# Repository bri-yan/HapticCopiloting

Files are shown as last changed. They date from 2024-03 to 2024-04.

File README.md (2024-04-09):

# HapticCopiloting
Codebase for UBC's ENPH-459 (Engineering Physics) Capstone Project: **Haptic Shared Control**

Demonstrating complex human-robot control through a 1 DOF haptic device featuring a BDC motor control system in live feedback with a virtual environment.

Authors: 
* Gavin Pringle
* Yousif El-Wishahy
* Sayeh Oloumi Yazdi
* Brian Yan

## Important Directories
- twiddlerino: source code for the ESP32 controller, python serial interface, unit tests and test scripts
- sim: MATLAB source code for modelling and simualtion of motor, sensors and controller
- virtual_demos : directory containing virtual demonstrations for shared control, demos implemented in pygame and interface with esp32 controller using the serial interface
- electrical: KiCad pcb project (libraries, schematics and layout) using the twiddlerino hardware, and the KiCad electrical schematic for the test bench

## Contents
 - [Project Overview](#project-overview) 
 - [Firmware Dev Environment](#firmware-dev-environment) 

## Project Overview

When dancing with a partner, forces and torques from each person influence the motion of the other. Each person’s motion is therefore partially controlled by themselves and partially controlled by their partner. 

This is similar to shared control of a robotic system, where the behaviour of a robot changes depending on the stiffness of the environment it is operating in. In our project, we explore shared control on simple robotic devices with the addition of a virtual environment that guides the user on when to give and when to take control.

### Twiddlerino System Diagram

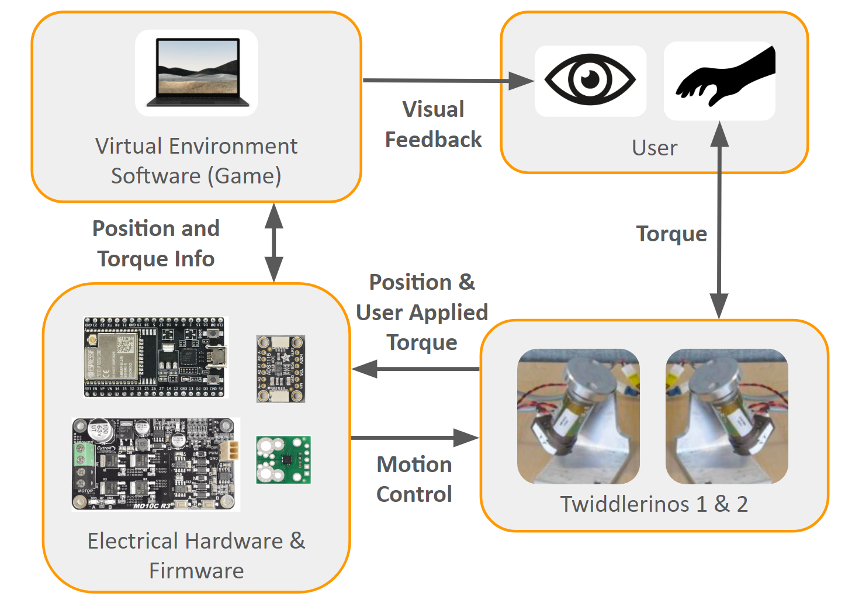
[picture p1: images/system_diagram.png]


### Control Theory

We have implemented shared control between a human and a robot by shifting between two existing controllers: impedance controllers and admittance controllers. Impedance and admittance controllers both simulate virtual spring-mass-damper systems. By shifting between these two controllers, the combined shared controller can act resistively and prevent changes to its trajectory or act compliantly and allow a person to dictate its trajectory.

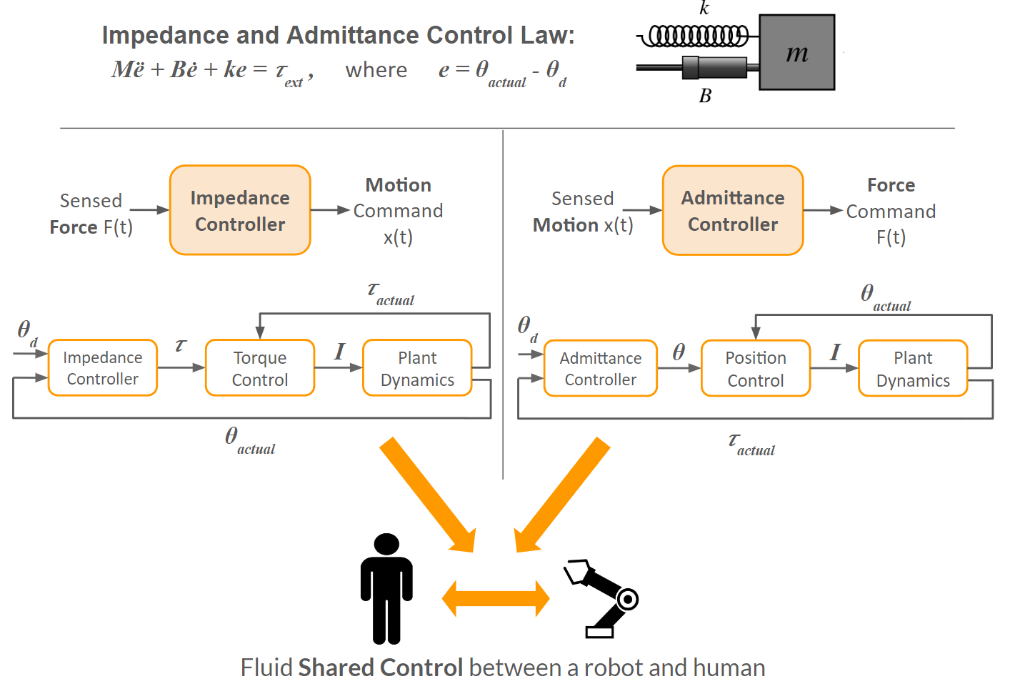
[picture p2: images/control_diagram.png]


### Defined Control Modes

Defined in control_type_t enum in the firmware:

| Control ID | Description |
|---|---|
| no_control | No actuator control is applied. Only telemetry is report. |
| position | Position PID control. Feedback is incremental encoder signal. |
| velocity | Velocity PID control. Feedback is rate of change of encoder signal. |
| torque | Current PID control to achieve torque control, uses linear relationship between current and torque.<br>Feedback is current sensor measurements. |
| impedance_spring | Cascaded controller. Inner loop runs current control with PID. <br>Outer loop applies a spring impedance law to determine desired current. <br>The linear friction torque (scales with velocity) is also accounted for in the impedance control law. |
| impedance_damping | Similar to imedance_spring but uses imedance damper law to compute current target. |
| impedance_spring_damping | Applies spring and damping impedance law. Has the effect of position and velocity impedance control. |
| impedance_ignore_t_ext | Applies full impedance law, but ignores external torques. |
| impedance | Applies full impedance law, and accounts for external torques.<br>External torque is estimated by comparing current measurements to an internal model the motor that estimates control current. |
| admittance | Applies full admittance law. This controller is also a cascaded controller.<br>The inner loop runs PID position control.<br>The outer loop runs an impedance control law to compute position. |

### Virtual Environment
The virtual environment guides the user on when to give and when to take control. The player  must control two twidderinos to ensure both player-controlled ships avoid all obstacles. Ships will automatically avoid asteroids but players must take action to avoid enemy projectiles.

Promoted Behaviour:
* Human-robot collaboration
* Shared common goal
* Awareness of robots actions

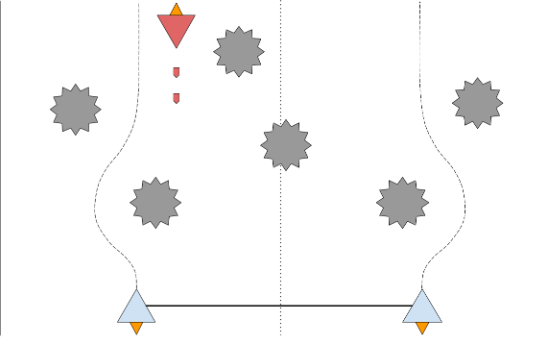
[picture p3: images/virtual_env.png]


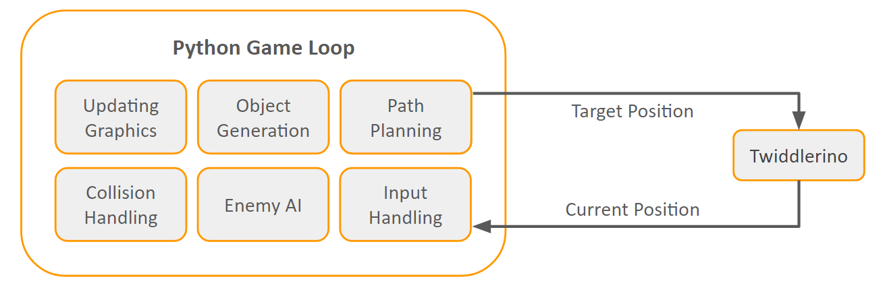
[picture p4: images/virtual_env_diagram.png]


### Hardware Architecture

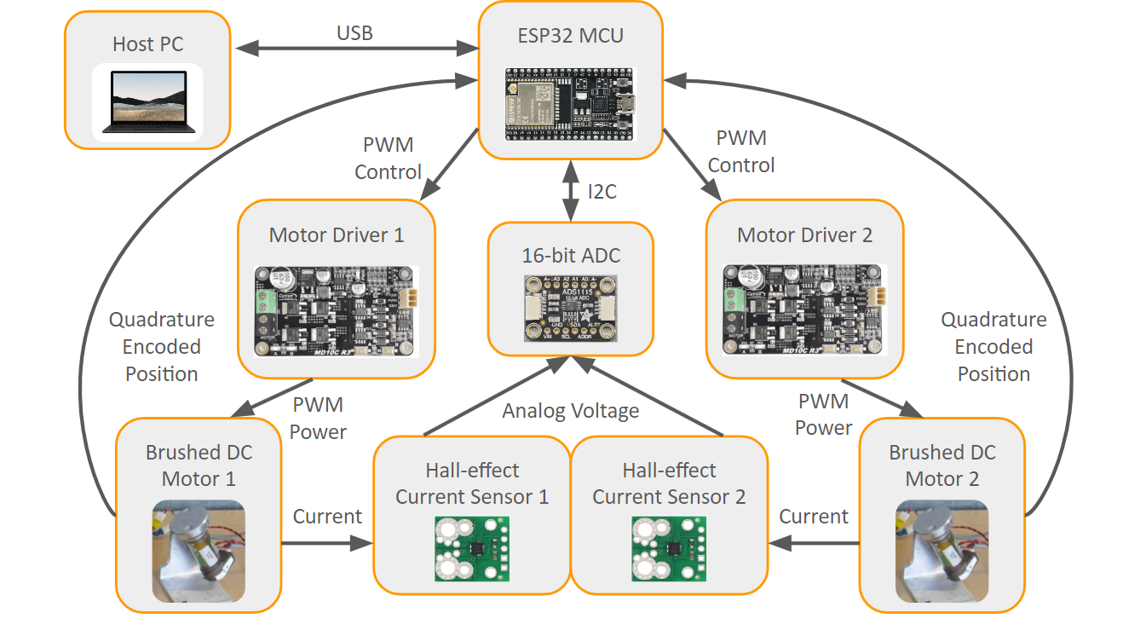
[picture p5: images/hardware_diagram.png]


### Firmware Architecure

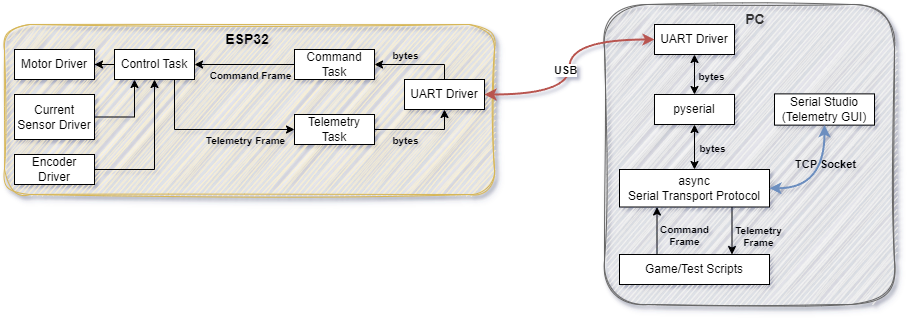
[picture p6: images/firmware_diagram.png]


## Firmware Dev Environment

[Refer to firmware diagram](#firmware-architecture)

Embedded development environment: [Platformio](https://platformio.org/) IDE plugin for VSCode

[Install platformio](https://platformio.org/)

config file: `twiddlerino/platformio.ini`

Directory structure

```bash
├───.pio
│   ├───build
│   └───libdeps
├───include
├───lib
├───python_tests
│   ├───data
│   └───serial_interface
├───src
│   ├───app
│   │   ├───calibration
│   │   ├───control
│   │   └───filter
│   └───drivers
└───test
```

## Serial Commmand & Telemetry Interface

Command and telemetry of the Twiddlerino system is achieved through telemetry and command frames (utf-8 encoded strings) sent over a USB port between the ESP32 and the HOST PC.

The ESP32 devkit has an onboard CP210X USB-to-UART module that converts the USB signal to a UART signal for the UART driver on the ESP32 to handle.

The serial protocol is implemented in C++ on esp32 and Python on Host PC.

[Refer to firmware diagram for details](#firmware-architecture)

### Telemetry Definition

[Serial Studio](https://serial-studio.github.io/), an open source telemetry GUI, is used to record and visualize system data during testing of the controller.

Telemetry frames are defined in a .JSON configuration file per the serial studio standard, see `twiddlerino/serial-studio-dashboard.json`.

Telemetry frame: `"/*TWIDDLERINO_TELEMETRY,%s,%s,...,%s*/"`

The firmware running on the ESP32 periodically sends telemetry strings over a serial port. The python serial protocol recieves the telemetry frames and sends them over a TCP socket to Serial Studio. 

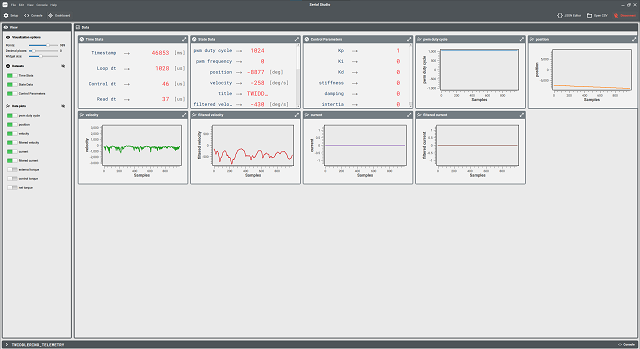
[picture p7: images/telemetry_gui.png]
Telemetry GUI


### Command Definition
Several commands are available to set parameters over the serial interface and to control the state of the controller.
**Each command is a newline terminated string.**

`"stop\n"` - Stops controller (telemetry also stops)

`"reset\n"` - Resets controller (configuration reverts to default)

`"reboot\n"` - Reboots the microcontroller! UART driver will not be affected.

`"telemetry_enable\n"` - Enable controller telemetry stream over serial (rate==`TELEMETRY_SAMPLES_PER_LOOP `)

`"telemetry_disable\n"` - Disable controller telemetry stream over serial (rate==`TELEMETRY_SAMPLES_PER_LOOP `)

`"set_pid,<controller_id(string)>,<double>,<double>,<double>,\n"` - Set P, I, and D values of PID controller

`"set_impedance,<controller_id(string)>,<double>,<double>,<double>,\n"` - Set stiffness, damping, and inertia values of impedane/admittance controller

`"set_mode,<controller_id(string)>,<string>,\n"` - Sets control mode, the string values represents an enum. Refer to the `control_type_t` struct definition in `twiddlerino/src/app/control/twid_control.h`.
* modes: `no_control`, `position`, `velocity`, `torque`, `impedance`, `impedance_spring`, `impedance_damping`, `impedance_spring_damping`, `impedance_ignore_t_ext`, `admittance`

`"set_setpoint,<controller_id(string)>,<double>,<double>,<double>,<double>,\n"` - Set position, velocity, acceleration and torque setpoints for the controller. 

`"set_dutycycle,<controller_id(string)>,<int>,\n"` - Sets motor duty cycle directly regardless of controller running.

`"set_telemsamplerate,<controller_id(string)>,<uint>,\n"` - Set telemetry sample rate in terms of (# control loops)/sample. I.e. how many control loops to wait before sending telemetry to serial queue.

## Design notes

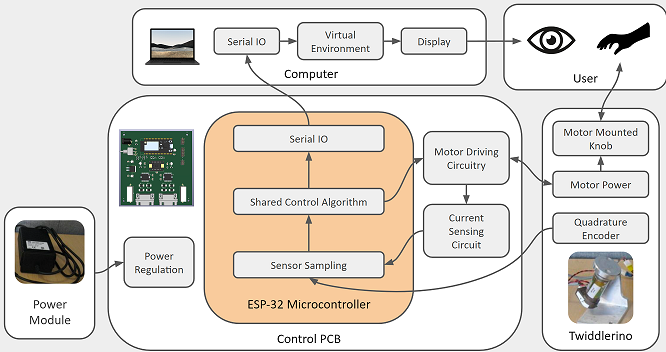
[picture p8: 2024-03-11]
system_diagram.png

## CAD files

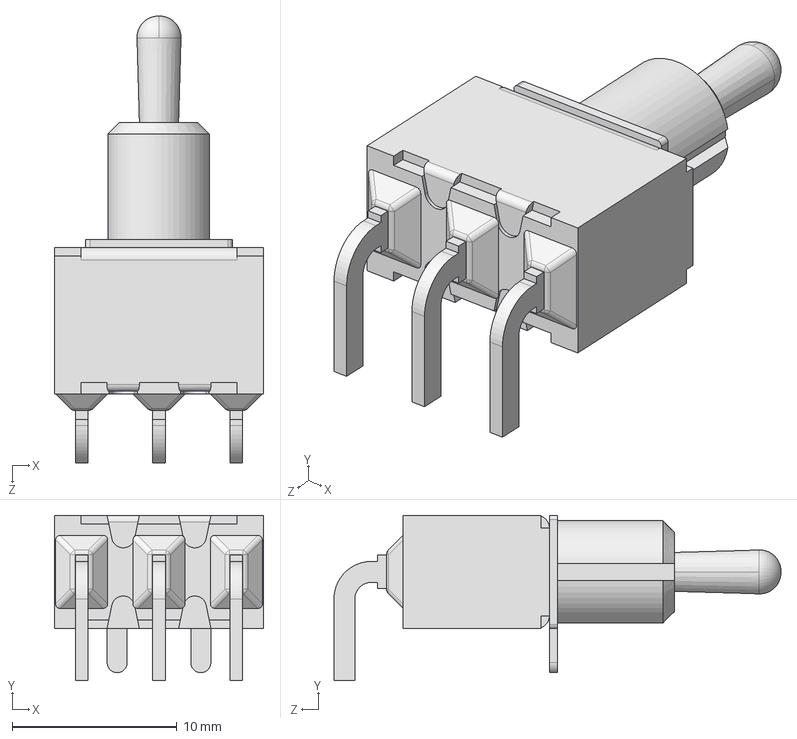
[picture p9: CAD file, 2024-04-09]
electrical/component_libs/100SP1T2B4M6QE/100SP1T2B4M6QE.step
12.7 x 10.0 x 27.2 mm

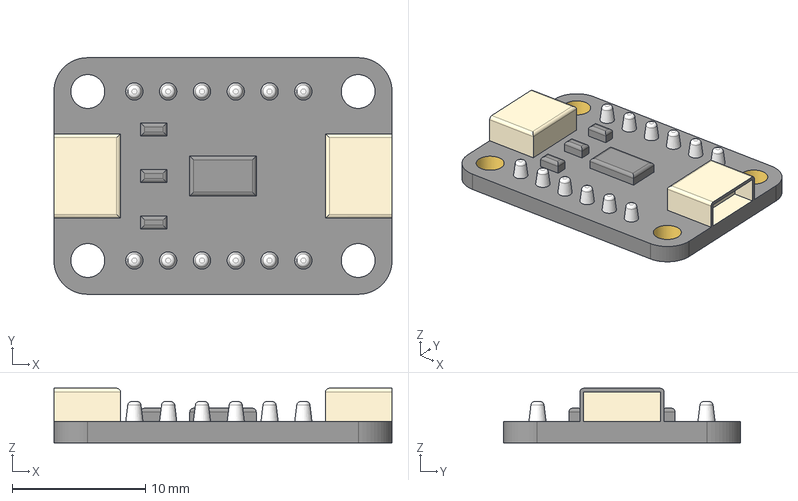
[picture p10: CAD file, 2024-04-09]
electrical/component_libs/adafruit_ads1115/adafruit_ads1115.step
25.4 x 17.8 x 4.10 mm

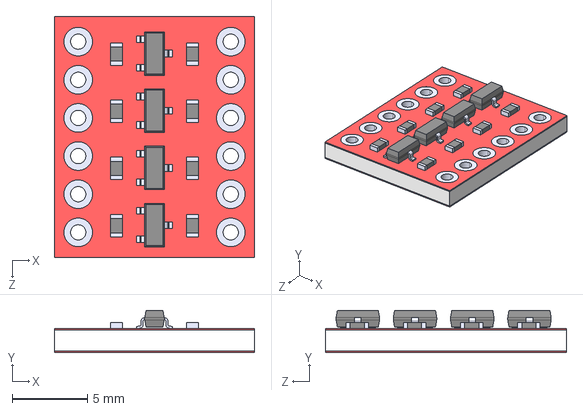
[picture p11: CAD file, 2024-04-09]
electrical/component_libs/BOB-12009/BOB-12009.step
13.3 x 2.80 x 16.1 mm

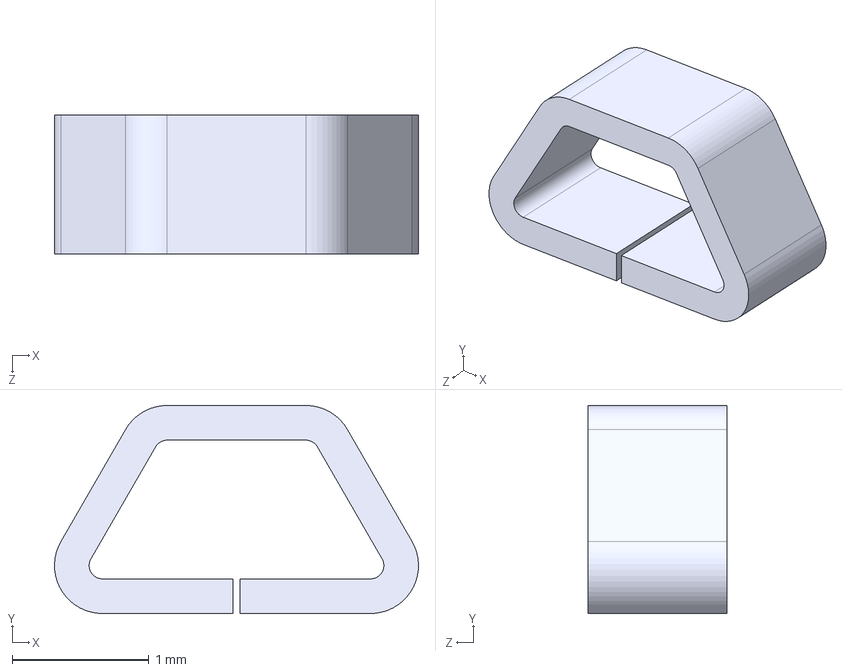
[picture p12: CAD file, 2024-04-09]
electrical/component_libs/Keystone5015/Keystone5015.STEP
2.67 x 1.52 x 1.02 mm

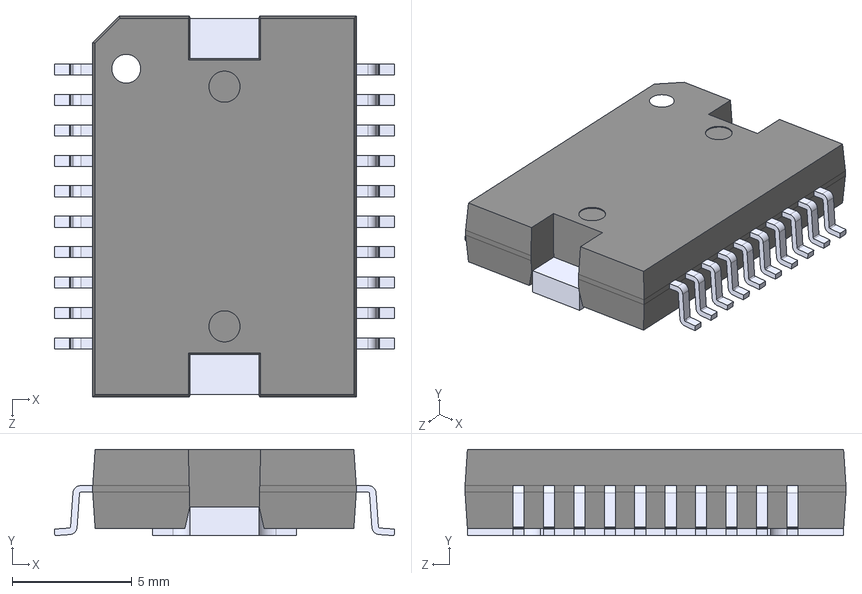
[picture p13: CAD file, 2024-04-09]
electrical/component_libs/L298P/L298P.step
14.2 x 3.60 x 15.9 mm

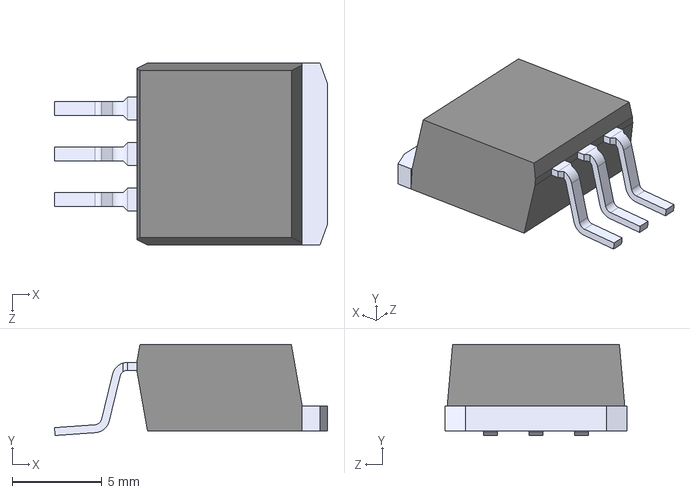
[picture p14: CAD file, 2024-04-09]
electrical/component_libs/LM340S-5/LM340S-5.step
15.2 x 5.08 x 10.2 mm

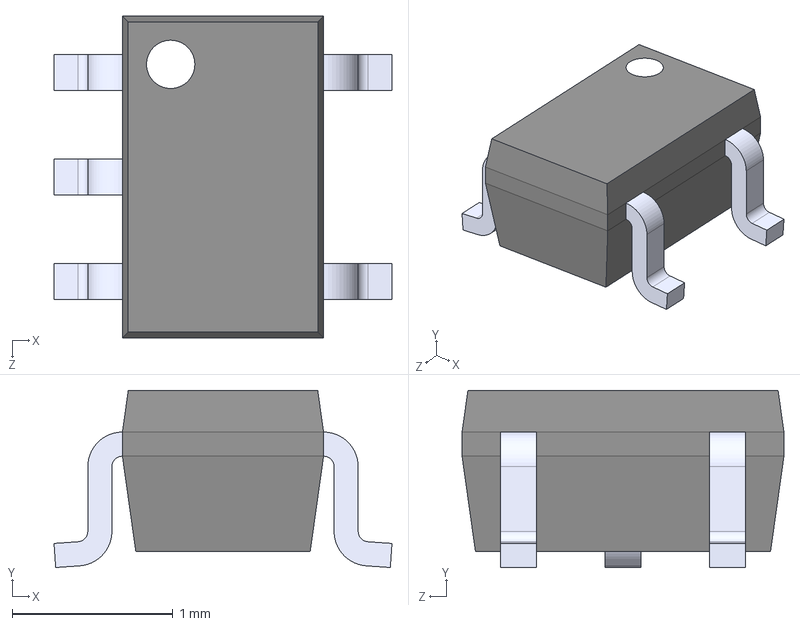
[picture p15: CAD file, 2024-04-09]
electrical/component_libs/OPA347SA_3K/OPA347SA_3K.step
2.10 x 1.10 x 2.00 mm

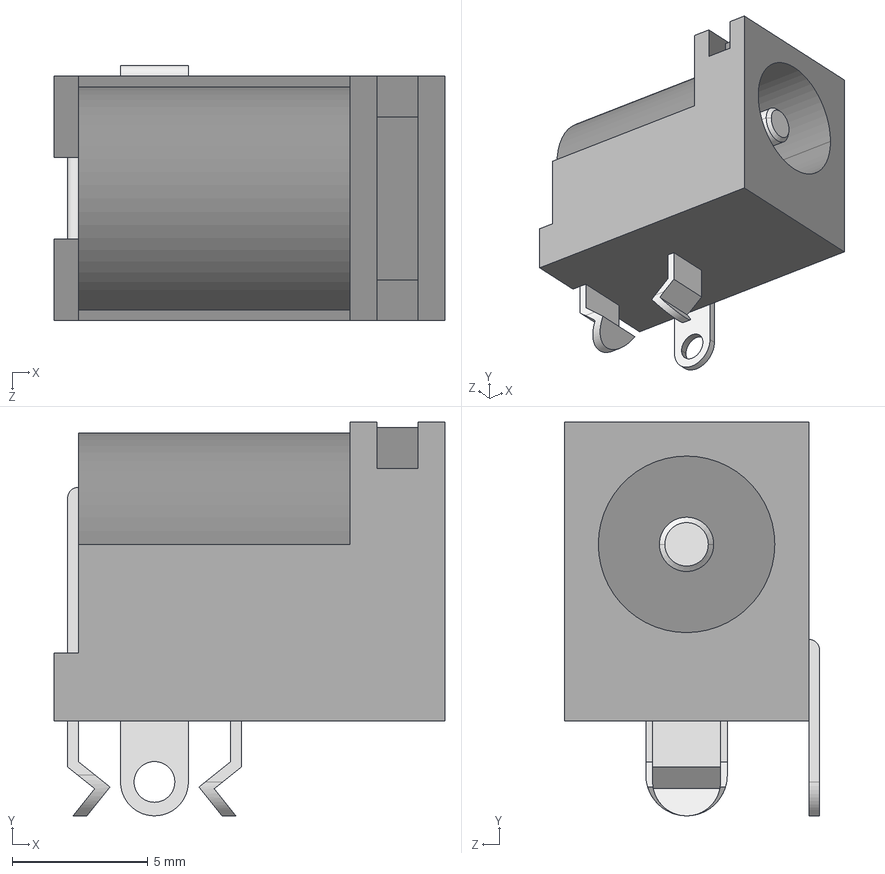
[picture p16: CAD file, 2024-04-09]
electrical/component_libs/PJ-202AH/CUI_DEVICES_PJ-202AH.step
14.4 x 14.5 x 9.40 mm

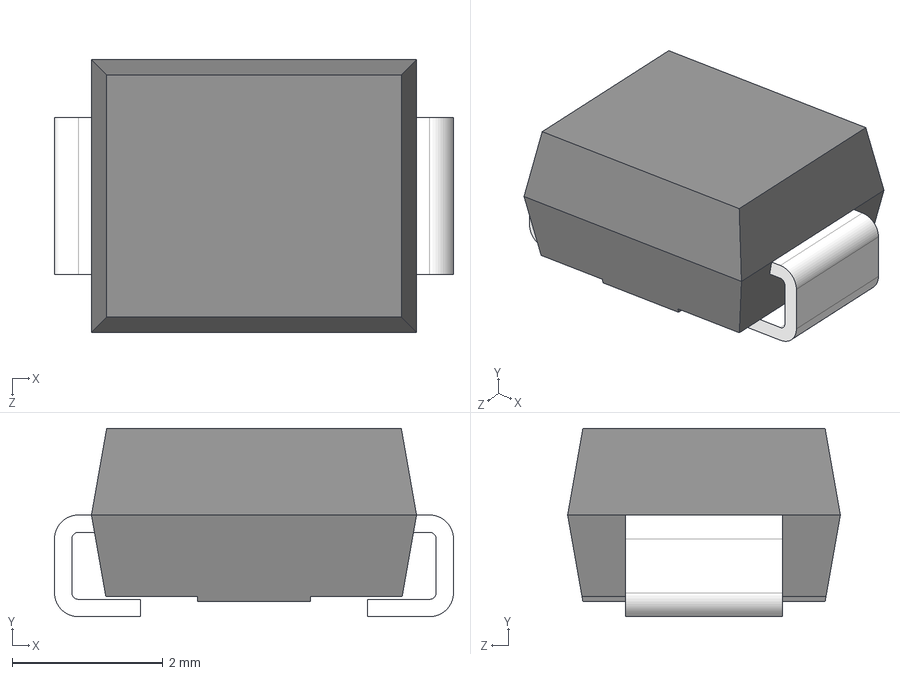
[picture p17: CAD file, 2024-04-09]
electrical/component_libs/RS3A-13-F/RS3A-13-F.step
5.30 x 2.50 x 3.62 mm

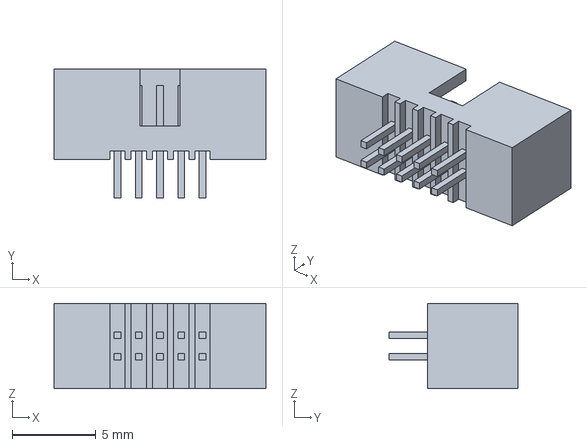
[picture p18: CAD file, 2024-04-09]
electrical/component_libs/20021511-00010T4LF/20021511-00010T4LF.step
12.7 x 7.70 x 5.10 mm

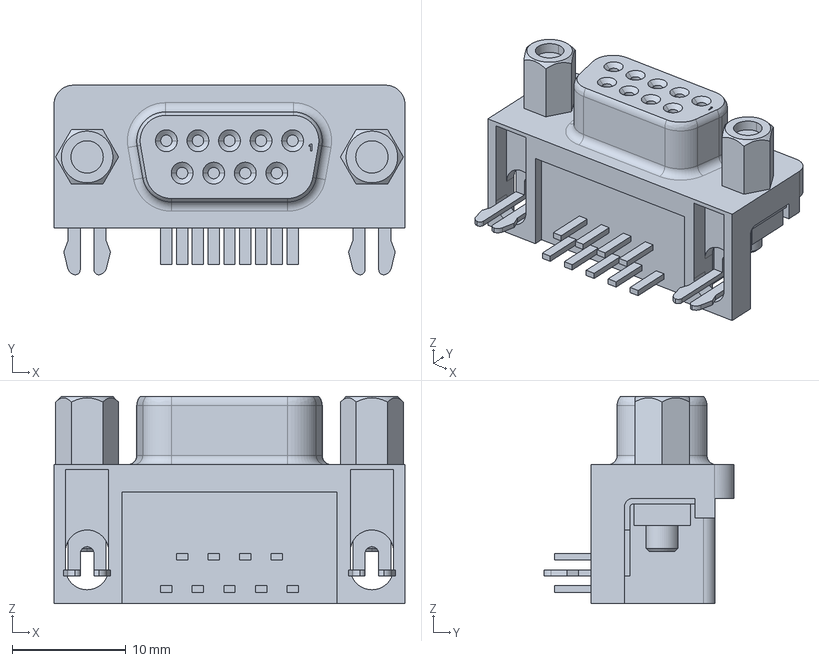
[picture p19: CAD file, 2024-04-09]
electrical/component_libs/2311765-1/2311765-1.step
30.8 x 16.6 x 18.2 mm

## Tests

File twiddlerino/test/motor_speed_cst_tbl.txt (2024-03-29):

dc
490.0,
495.0,
500.0,
506.0,
511.0,
516.0,
522.0,
527.0,
533.0,
538.0,
543.0,
549.0,
554.0,
560.0,
565.0,
570.0,
576.0,
581.0,
587.0,
592.0,
597.0,
603.0,
608.0,
614.0,
619.0,
624.0,
630.0,
635.0,
641.0,
646.0,
651.0,
657.0,
662.0,
668.0,
673.0,
678.0,
684.0,
689.0,
694.0,
700.0,
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
volts_approx
5.7421875,
5.80078125,
5.859375,
5.9296875,
5.98828125,
6.046875,
6.1171875,
6.17578125,
6.24609375,
6.3046875,
6.36328125,
6.43359375,
6.4921875,
6.5625,
6.62109375,
6.6796875,
6.75,
6.80859375,
6.87890625,
6.9375,
6.99609375,
7.06640625,
7.125,
7.1953125,
7.25390625,
7.3125,
7.3828125,
7.44140625,
7.51171875,
7.5703125,
7.62890625,
7.69921875,
7.7578125,
7.828125,
7.88671875,
7.9453125,
8.015625,
8.07421875,
8.1328125,
8.203125,
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
current
0.159187,
0.133125,
0.1395,
0.136688,
0.131625,
0.133313,
0.144562,
0.155062,
0.143063,
0.1485,
0.143813,
0.144375,
0.15225,
0.1545,
0.153563,
0.164625,
0.162375,
0.15525,
0.168938,
0.16125,
0.162938,
0.167438,
0.17175,
0.178125,
0.178312,
0.175125,
0.17325,
0.179438,
0.178875,
0.180375,
0.183375,
0.178312,
0.18375,
0.182625,
0.190313,
0.186937,
0.192188,
0.19125,
0.192938,
0.193687,
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
vel_filtered
12.968628837354,
24.3714350746476,
33.2487898171962,
41.5701308022924,
49.8356703758814,
57.6959549001702,
66.1900503590898,
74.36253790807501,
83.0116520766108,
91.377109419051,
99.9637825218804,
108.49980967367641,
116.746442820414,
125.1817082664906,
133.8068142689586,
141.9745308885756,
151.1072048604606,
159.0463129206876,
167.3490344111844,
175.8605258185602,
183.9147956042046,
193.2027904023288,
202.2435127452684,
211.4056059647268,
220.346972465262,
229.5234294713676,
238.73276116428718,
247.52061273153421,
255.99656967389578,
263.483626338357,
271.67072732599263,
279.3544512306072,
287.6387007767028,
297.29117828415656,
307.3967208750402,
317.1400195611984,
328.2603700037826,
338.6205349137336,
348.95609454531717,
360.9387905497434,
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
i_rpm
v_rpm
Ke
38.11784627294291,
R
0.0030723654445421814,

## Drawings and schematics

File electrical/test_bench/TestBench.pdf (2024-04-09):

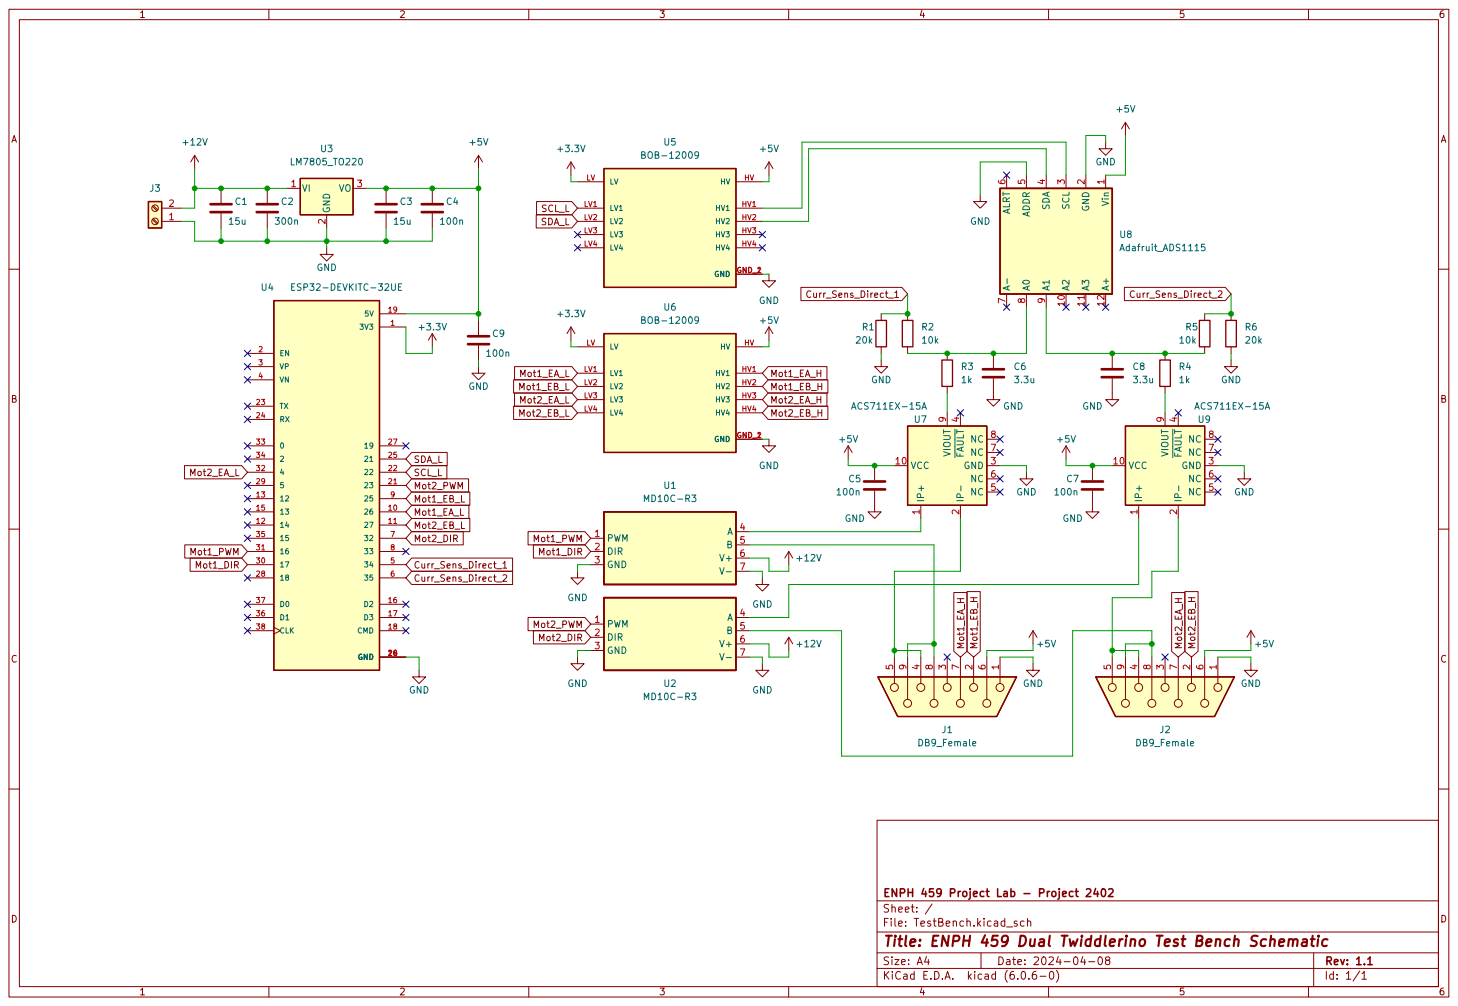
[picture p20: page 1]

4 NC 5 NC 6 NC 7 NC 8 VIOUT U7 9 ACS711EX-15A
+5VGND

4 NC 5 NC 6 NC 7 NC 8 VIOUT

1 VCC 10 IP- 2 GND ~{FAULT} 3

Id: 1/1 Title: ENPH 459 Dual Twiddlerino Test Bench Schematic

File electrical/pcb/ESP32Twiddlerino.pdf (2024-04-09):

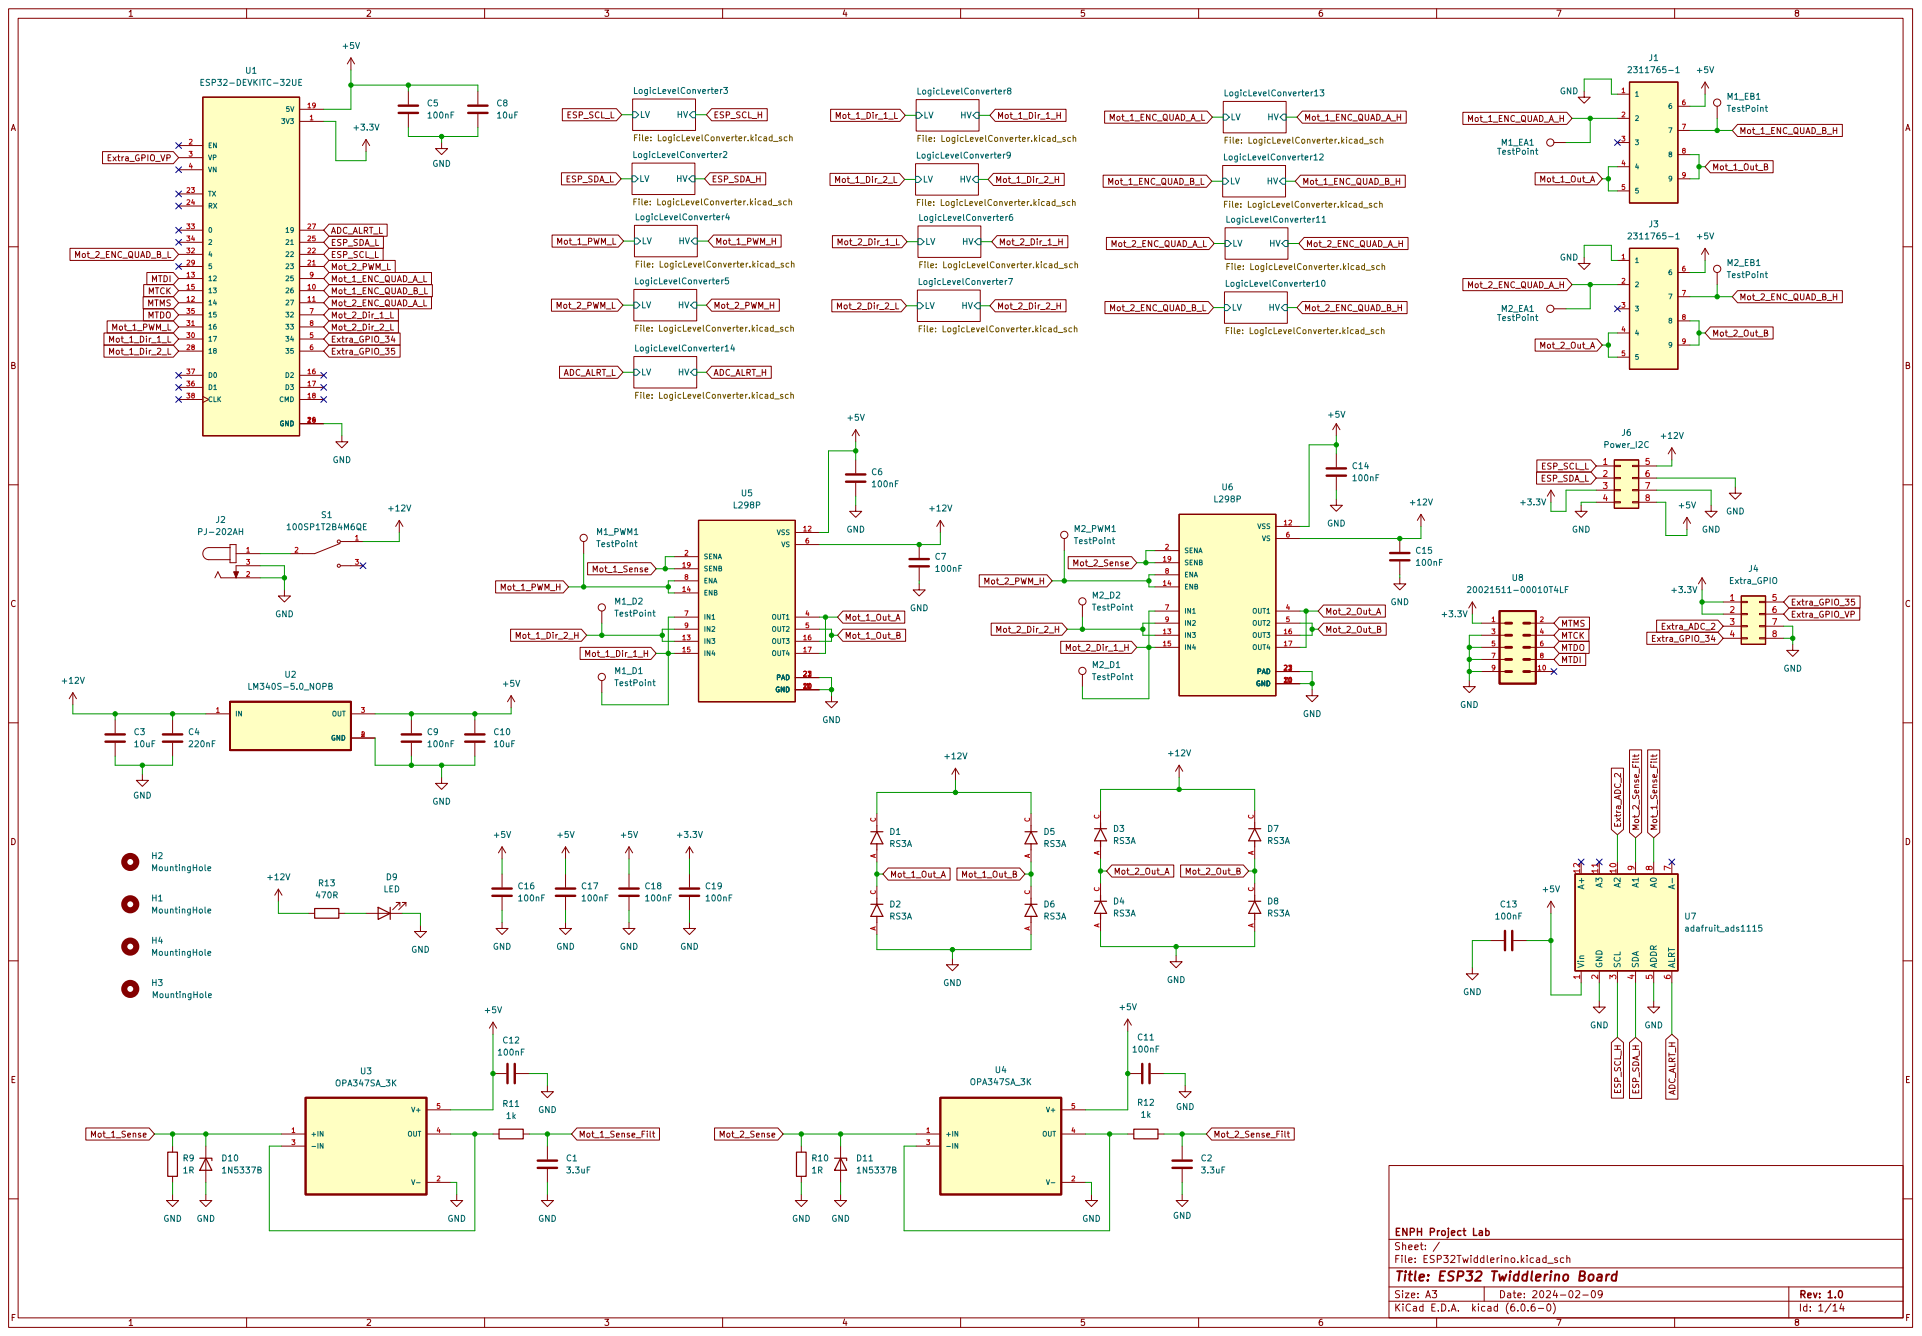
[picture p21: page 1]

File: ESP32Twiddlerino.kicad_sch Sheet: / ENPH Project Lab

Id: 1/14 Title: ESP32 Twiddlerino Board

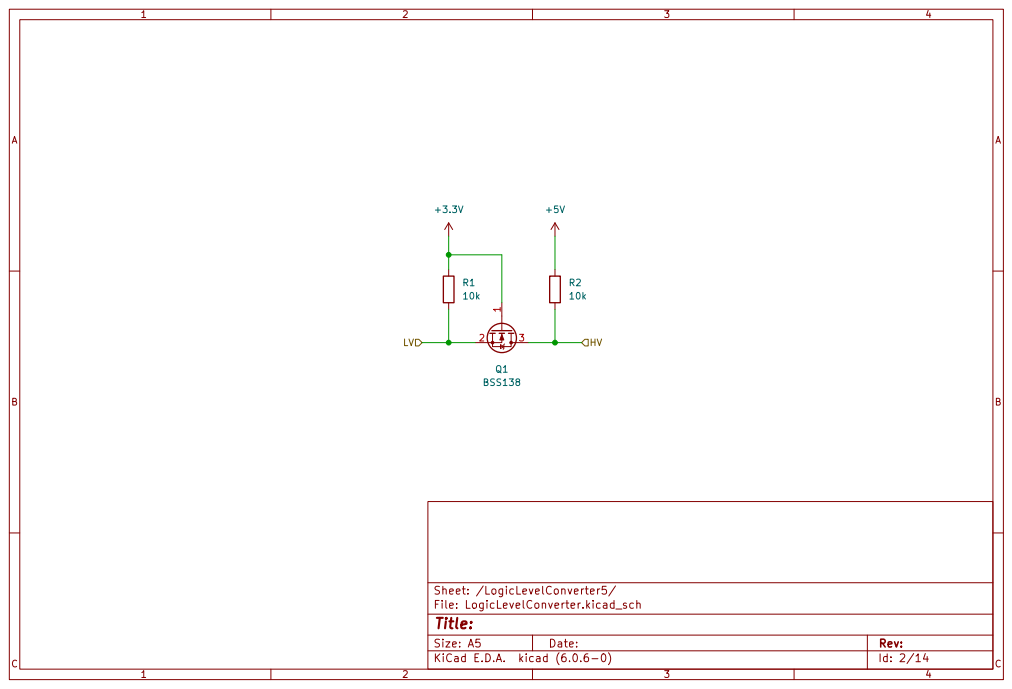
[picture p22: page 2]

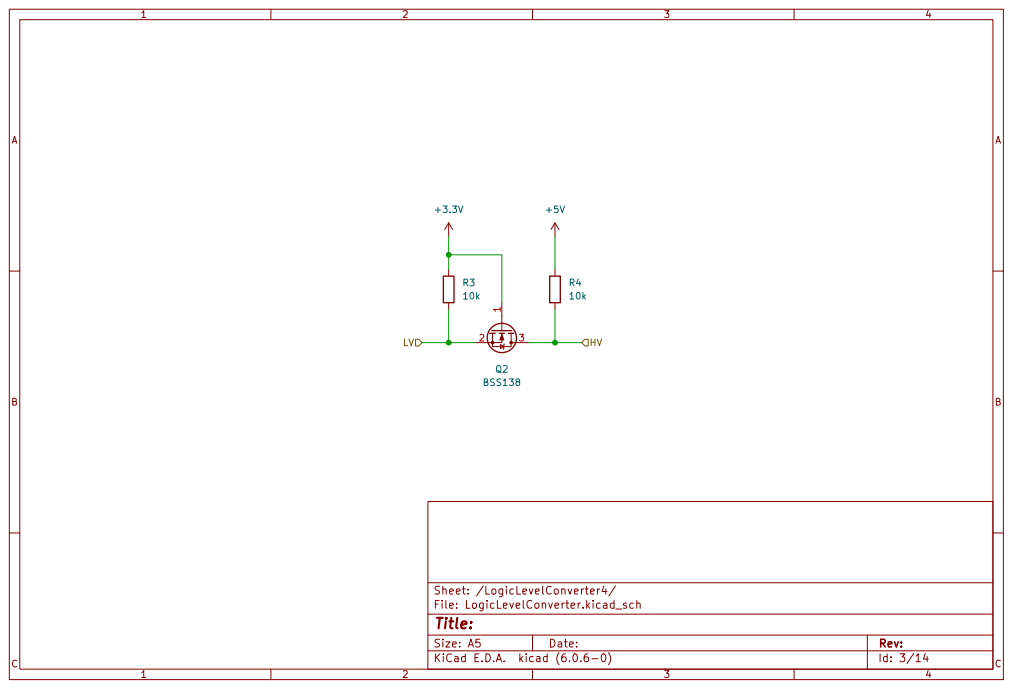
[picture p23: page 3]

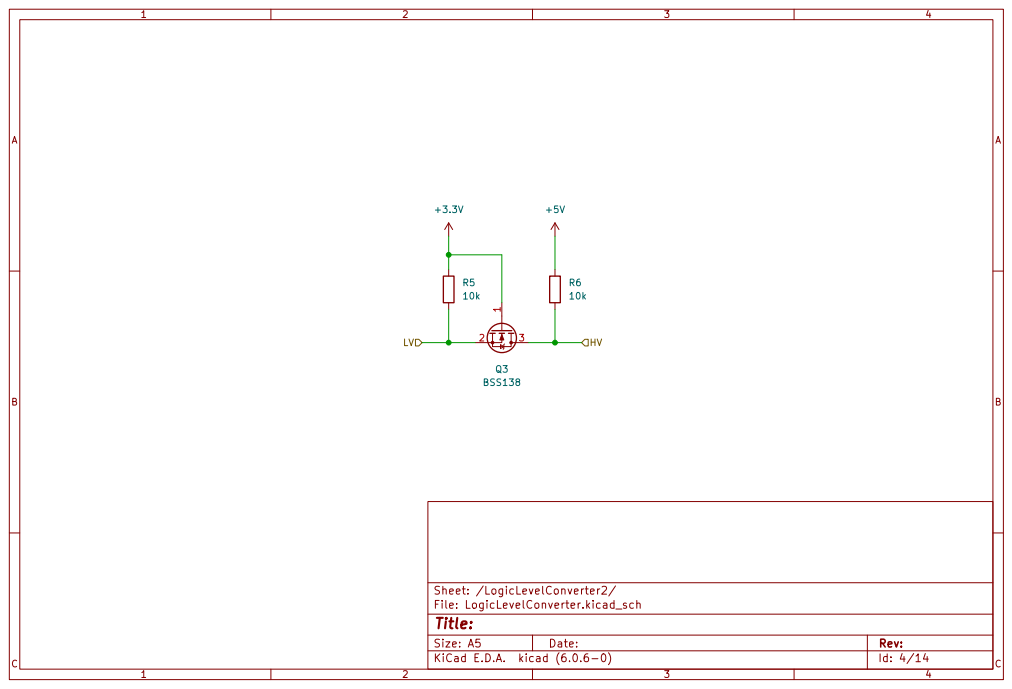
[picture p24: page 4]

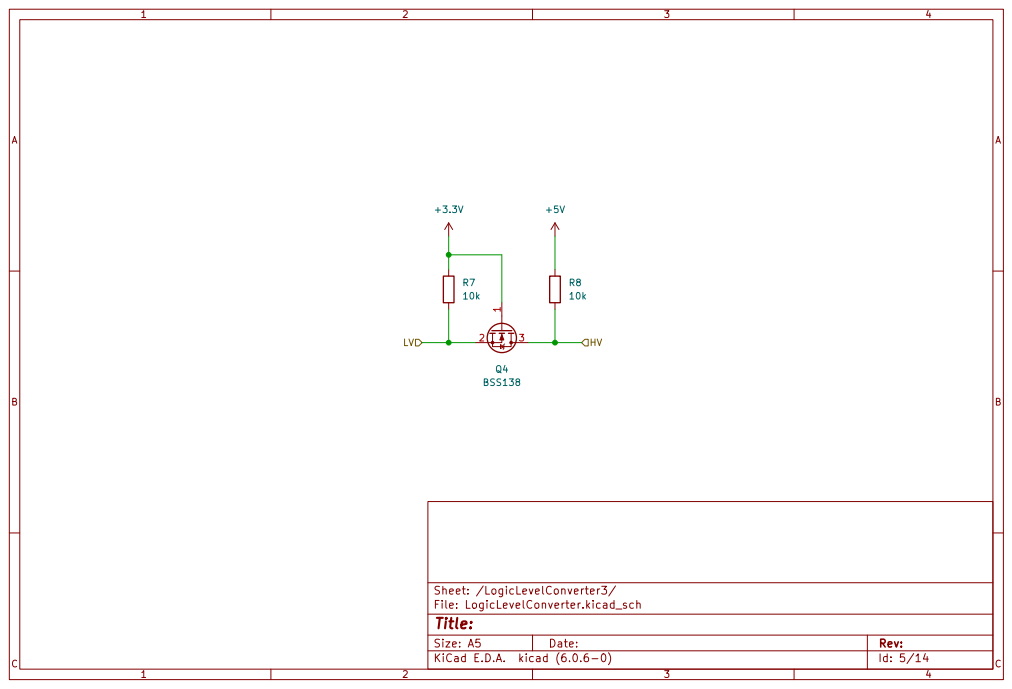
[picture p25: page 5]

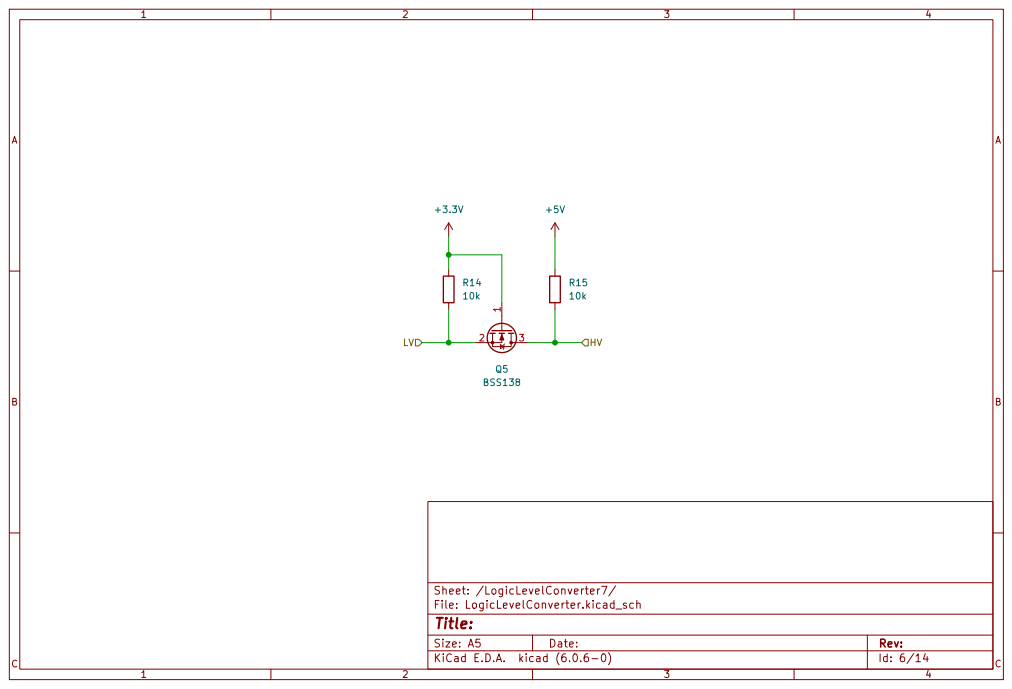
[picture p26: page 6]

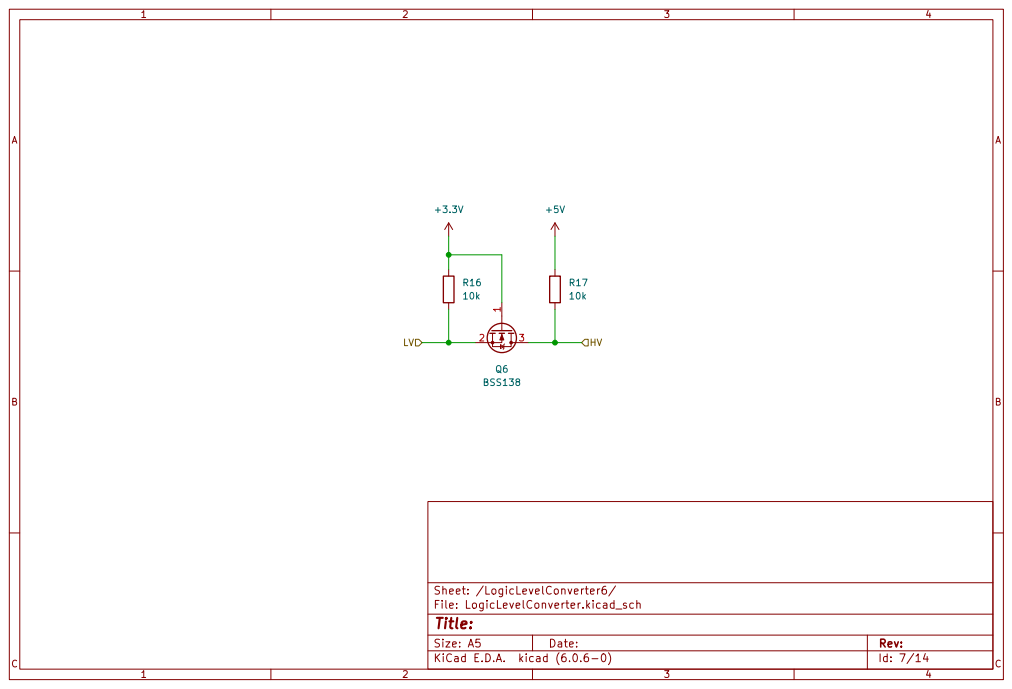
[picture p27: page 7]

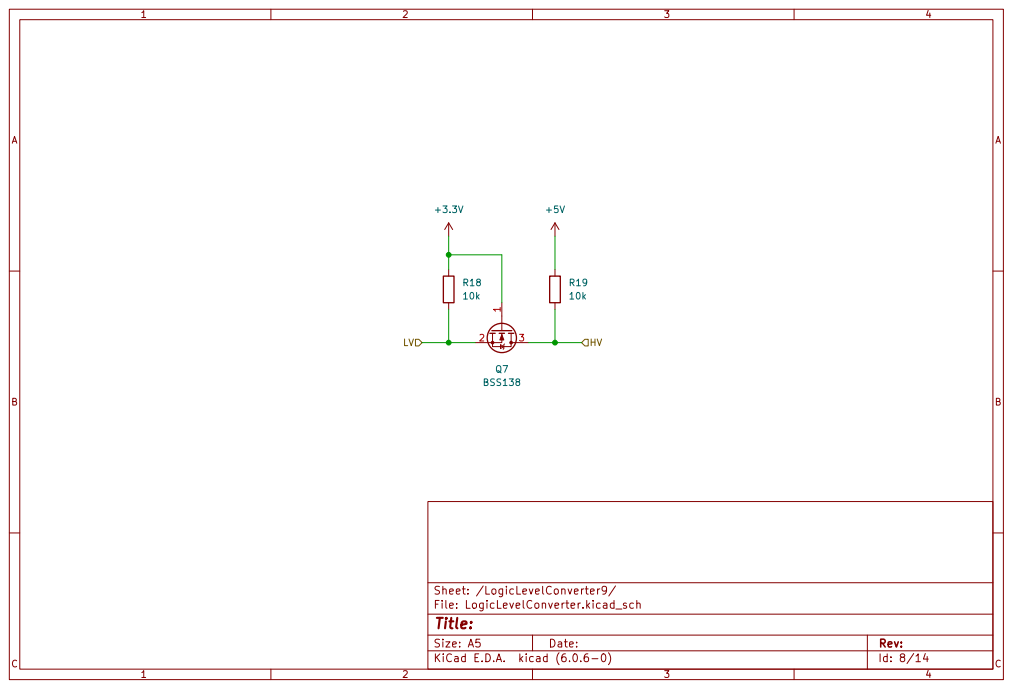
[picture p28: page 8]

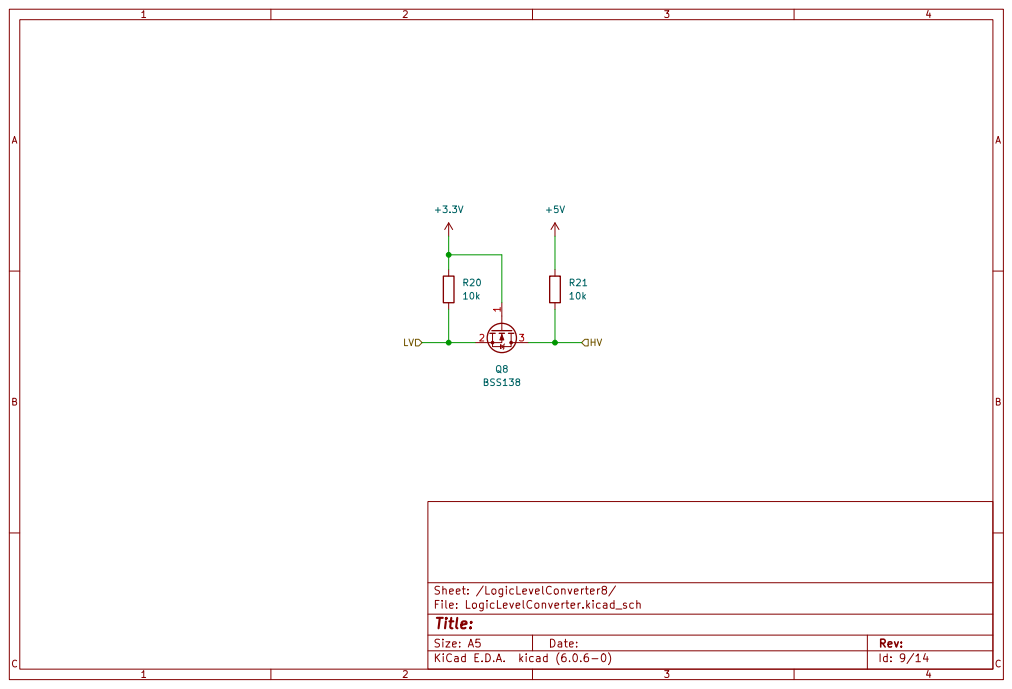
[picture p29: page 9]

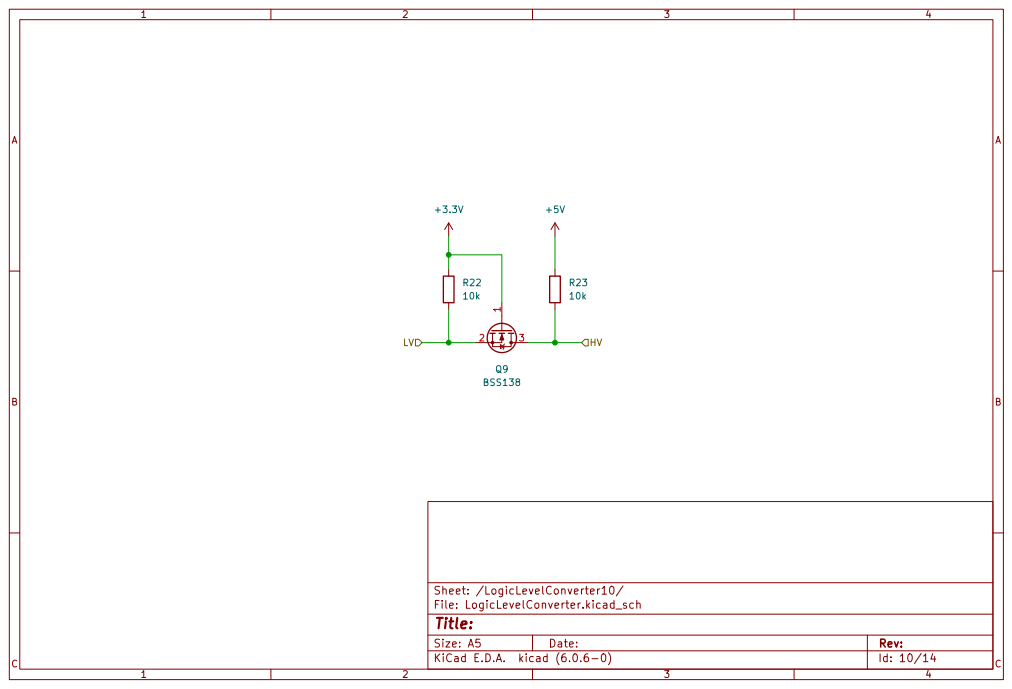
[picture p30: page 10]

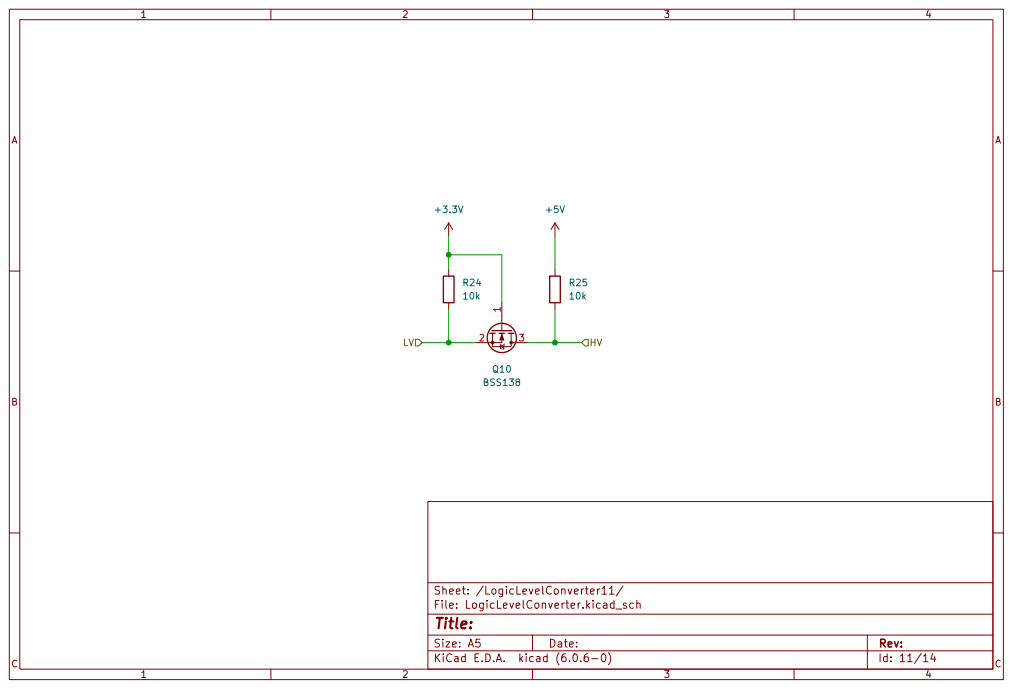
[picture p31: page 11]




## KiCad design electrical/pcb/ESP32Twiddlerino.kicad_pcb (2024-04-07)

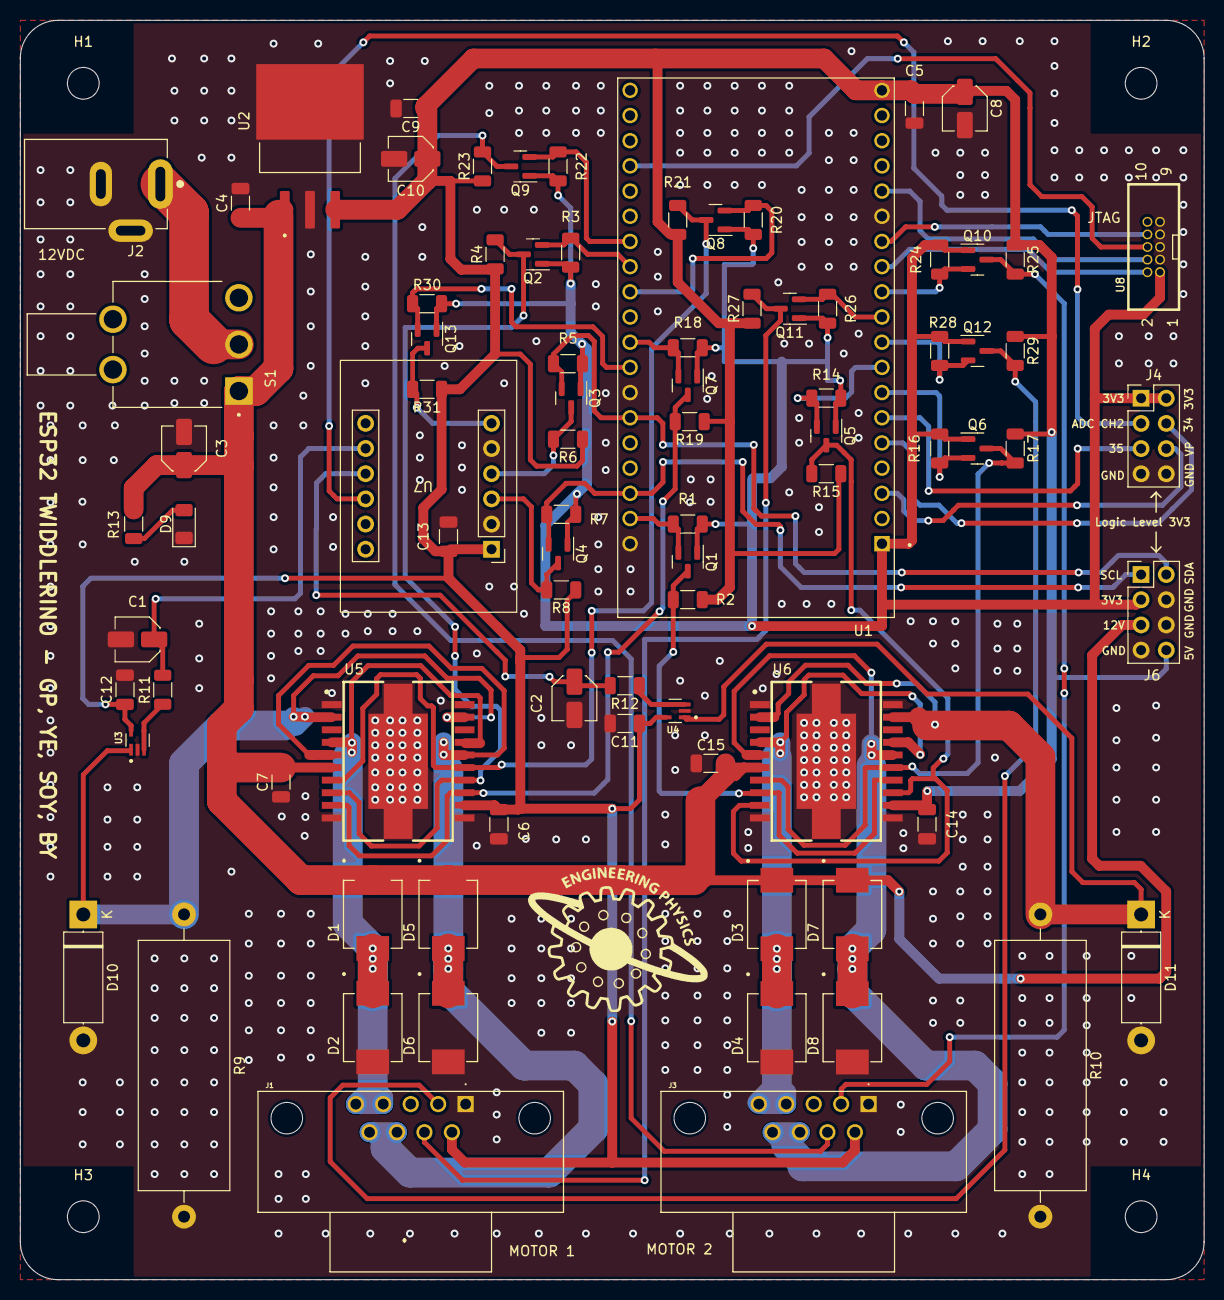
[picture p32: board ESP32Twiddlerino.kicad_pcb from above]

Board: 2 copper layers, 119.4 x 127.0 mm, 89 parts (0 on the bottom side), 50 nets.

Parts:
.: LOGO
C1, C2: 3.3uF; C_Elec_4x5.4
C3, C8, C10: 10uF; C_Elec_4x5.4
C4: 220nF; C_1206_3216Metric
C5, C6, C7, C9, C11, C12, C13, C14, C15: 100nF; C_1206_3216Metric
D1, D2, D3, D4, D5, D6, D7, D8: RS3A; RS3A-13-F
D9: LED; LED_1206_3216Metric
D10, D11: 1N5337B; D_5W_P12.70mm_Horizontal
H1, H2, H3, H4: MountingHole; MountingHole_3.2mm_M3
J1, J3: 2311765-1; TE_2311765-1
J2: PJ-202AH; CUI_PJ-202AH
J4: Extra_GPIO; PinHeader_2x04_P2.54mm_Vertical
J6: Power_I2C; PinHeader_2x04_P2.54mm_Vertical
Q1, Q2, Q3, Q4, Q5, Q6, Q7, Q8, Q9, Q10, Q11, Q12, Q13: BSS138; SOT-23
R1, R2, R3, R4, R5, R6, R7, R8, R14, R15, R16, R17, R18, R19, R20, R21, R22, R23, R24, R25, R26, R27, R28, R29, R30, R31: 10k; R_1206_3216Metric
R9, R10: 1R; R_Axial_Power_L25.0mm_W9.0mm_P30.48mm
R11, R12: 1k; R_1206_3216Metric
R13: 470R; R_1206_3216Metric
S1: 100SP1T2B4M6QE; SW_100SP1T2B4M6QE
U1: ESP32-DEVKITC-32UE; ESPRESSIF_ESP32-DEVKITC-32UE
U2: LM340S-5.0_NOPB; LM340S-5
U3, U4: OPA347SA_3K; SOT65P210X110-5N
U5, U6: L298P
U7: adafruit_ads1115
U8: 20021511-00010T4LF

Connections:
+3.3V: J4.1, J4.2, J6.3, Q1.1 (G), Q2.1 (G), Q3.1 (G), Q4.1 (G), Q5.1 (G), Q6.1 (G), Q7.1 (G), Q8.1 (G), Q9.1 (G), Q10.1 (G), Q11.1 (G), Q12.1 (G), Q13.1 (G), R1.1, R3.1, R5.1, R7.1, R14.1, R16.1, R18.1, R20.1, R22.1, R24.1, R26.1, R28.1, R30.1, U1.1 (3V3), U8.1
+5V: C5.2, C6.2, C8.1, C9.1, C10.1, C11.1, C12.1, C13.2, C14.2, J1.6, J3.6, J6.8, R2.1, R4.1, R6.1, R8.1, R15.1, R17.1, R19.1, R21.1, R23.1, R25.1, R27.1, R29.1, R31.1, U1.19 (5V), U2.3 (OUT), U3.5 (V+), U4.5 (V+), U5.12 (VSS), U6.12 (VSS), U7.1 (Vin)
+12V: C3.1, C4.1, C7.2, C15.2, D1.C, D3.C, D5.C, D7.C, J6.5, R13.1, S1.1, U2.1 (IN), U5.6 (VS), U6.6 (VS)
ADC_ALRT_H: Q13.3 (D), R31.2, U7.6 (ALRT)
ADC_ALRT_L: Q13.2 (S), R30.2, U1.27 (19)
ESP_SCL_H: Q4.3 (D), R8.2, U7.3 (SCL)
ESP_SCL_L: J6.1, Q4.2 (S), R7.2, U1.22
ESP_SDA_H: Q3.3 (D), R6.2, U7.4 (SDA)
ESP_SDA_L: J6.2, Q3.2 (S), R5.2, U1.25 (21)
Extra_ADC_2: J4.3, U7.10 (A2)
Extra_GPIO_34: J4.4, U1.5 (34)
Extra_GPIO_35: J4.5, U1.6 (35)
Extra_GPIO_VP: J4.6, U1.3 (VP)
GND: C1.2, C2.2, C3.2, C4.2, C5.1, C6.1, C7.1, C8.2, C9.2, C10.2, C11.2, C12.2, C13.1, C14.1, C15.1, D2.A, D4.A, D6.A, D8.A, D9.1 (K), D10.2 (A), D11.2 (A), J1.1, J2.2, J2.3, J3.1, J4.7, J4.8, J6.4, J6.6, J6.7, R9.2, R10.2, U1.14 (GND), U1.20 (GND), U1.26 (GND), U2.2 (GND), U2.4 (GND), U3.2 (V-), U4.2 (V-), U5.1 (GND), U5.10 (GND), U5.11 (GND), U5.20 (GND), U5.21 (PAD), U5.22 (PAD), U5.23 (PAD), U6.1 (GND), U6.10 (GND), U6.11 (GND), U6.20 (GND), U6.21 (PAD), U6.22 (PAD), U6.23 (PAD), U7.2 (GND), U7.5 (ADDR), U8.3, U8.5, U8.7, U8.9
MTCK: U1.15 (13), U8.4
MTDI: U1.13 (12), U8.8
MTDO: U1.35 (15), U8.6
MTMS: U1.12 (14), U8.2
Mot_1_Dir_1_H: Q8.3 (D), R21.2, U5.7 (IN1), U5.15 (IN4)
Mot_1_Dir_1_L: Q8.2 (S), R20.2, U1.30 (17)
Mot_1_Dir_2_H: Q7.3 (D), R19.2, U5.9 (IN2), U5.13 (IN3)
Mot_1_Dir_2_L: Q7.2 (S), R18.2, U1.28 (18)
Mot_1_ENC_QUAD_A_H: J1.2, Q12.3 (D), R29.2
Mot_1_ENC_QUAD_A_L: Q12.2 (S), R28.2, U1.9 (25)
Mot_1_ENC_QUAD_B_H: J1.7, Q11.3 (D), R27.2
Mot_1_ENC_QUAD_B_L: Q11.2 (S), R26.2, U1.10 (26)
Mot_1_Out_A: D1.A, D2.C, J1.4, J1.5, U5.4 (OUT1), U5.17 (OUT4)
Mot_1_Out_B: D5.A, D6.C, J1.8, J1.9, U5.5 (OUT2), U5.16 (OUT3)
Mot_1_PWM_H: Q2.3 (D), R4.2, U5.8 (ENA), U5.14 (ENB)
Mot_1_PWM_L: Q2.2 (S), R3.2, U1.31 (16)
Mot_1_Sense: D10.1 (K), R9.1, U3.1 (+IN), U5.2 (SENA), U5.19 (SENB)
Mot_1_Sense_Filt: C1.1, R11.2, U7.8 (A0)
Mot_2_Dir_1_H: Q6.3 (D), R17.2, U6.7 (IN1), U6.15 (IN4)
Mot_2_Dir_1_L: Q6.2 (S), R16.2, U1.7 (32)
Mot_2_Dir_2_H: Q5.3 (D), R15.2, U6.9 (IN2), U6.13 (IN3)
Mot_2_Dir_2_L: Q5.2 (S), R14.2, U1.8 (33)
Mot_2_ENC_QUAD_A_H: J3.2, Q10.3 (D), R25.2
Mot_2_ENC_QUAD_A_L: Q10.2 (S), R24.2, U1.11 (27)
Mot_2_ENC_QUAD_B_H: J3.7, Q9.3 (D), R23.2
Mot_2_ENC_QUAD_B_L: Q9.2 (S), R22.2, U1.32 (4)
Mot_2_Out_A: D3.A, D4.C, J3.4, J3.5, U6.4 (OUT1), U6.17 (OUT4)
Mot_2_Out_B: D7.A, D8.C, J3.8, J3.9, U6.5 (OUT2), U6.16 (OUT3)
Mot_2_PWM_H: Q1.3 (D), R2.2, U6.8 (ENA), U6.14 (ENB)
Mot_2_PWM_L: Q1.2 (S), R1.2, U1.21 (23)
Mot_2_Sense: D11.1 (K), R10.1, U4.1 (+IN), U6.2 (SENA), U6.19 (SENB)
Mot_2_Sense_Filt: C2.1, R12.2, U7.9 (A1)
unnamed: D9.2 (A), R13.2
unnamed: J2.1, S1.2
unnamed: R11.1, U3.3 (-IN), U3.4 (OUT)
unnamed: R12.1, U4.3 (-IN), U4.4 (OUT)

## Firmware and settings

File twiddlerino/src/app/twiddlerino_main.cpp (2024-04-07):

/**
 * @file twiddlerino.h
 * @brief Twiddlerino main file
 * @author Yousif El-Wishahy (ywishahy@student.ubc.ca)
 */

/******************************************************************************/
/*                              I N C L U D E S                               */
/******************************************************************************/

//header
#include "app/twiddlerino_main.h"

//twiddler pin definitions
#include "app/twid32_pin_defs.h"

//default configuration
#include "app/twid32_config.h"

//hardware drivers
#include "drivers/encoder.h"
#include "drivers/motor.h"
#include "drivers/current_sensor.h"

//telemetry and control
#include "comms.h"
#include "app/control/twid_control.h"

//arduino
#include "Arduino.h"


/******************************************************************************/
/*                               D E F I N E S                                */
/******************************************************************************/

/******************************************************************************/
/*                              T Y P E D E F S                               */
/******************************************************************************/

// Typedefs that are only used in this file, empty for now

/******************************************************************************/
/*            P R I V A T E  F U N C T I O N  P R O T O T Y P E S             */
/******************************************************************************/

//freertos tasks
void TaskPublishTelemetry(void *pvParameters);
void TaskRunTControl(void *pvParameters);
void TaskReadTCommands(void *pvParameters);

/******************************************************************************/
/*               P R I V A T E  G L O B A L  V A R I A B L E S                */
/******************************************************************************/
static const char* TAG = "twiddlerino_main";

static QueueHandle_t xQueueTelemetry;

static TaskHandle_t xTelemTask;
static TaskHandle_t xCommandTask;
static TaskHandle_t xTControlTask;

static bool enable_debug_telemetry = ENABLE_DEBUG_TELEMETRY_ON_INIT;

/******************************************************************************/
/*                P U B L I C  G L O B A L  V A R I A B L E S                 */
/******************************************************************************/

// Global variable definitions matching the extern definitions in the header

/******************************************************************************/
/*                       P U B L I C  F U N C T I O N S                       */
/******************************************************************************/

void twiddlerino_setup() {
  if(!Serial) {
    Serial.begin( UART_BAUD_RATE );//this is on rx0 tx0
    ESP_LOGI(TAG, "Serial connected on uart0! with baud rate %lu\n",UART_BAUD_RATE);
  }

  //queues for communicating with the control core
  xQueueTelemetry = xQueueCreate(TELEMETRY_QUEUE_SIZE, sizeof(telemetry_t));

  //hardware setup
  ESP_LOGI(TAG, "Hardware setup started");

  //setup hardware handles
  motor1_handle = {
    .power_pin = PIN_MOTOR1_POWER,
    .dir_pin = PIN_MOTOR1_DIR,
    .pwm_channel = MOTOR1_PWM_CHAN_DEFAULT,
    .state = motor_state_t::MOTOR_NOT_INITIALIZED,
    .handle_name = "motor1"
    };

  motor2_handle = {
    .power_pin = PIN_MOTOR2_POWER,
    .dir_pin = PIN_MOTOR2_DIR,
    .pwm_channel = MOTOR2_PWM_CHAN_DEFAULT,
    .state = motor_state_t::MOTOR_NOT_INITIALIZED,
    .handle_name = "motor2"
    };

  encoder1_handle = {
    .quad_pin_a = PIN_ENCODER1_QUAD_A,
    .quad_pin_b = PIN_ENCODER1_QUAD_B,
    .pcnt_unit = pcnt_unit_t::PCNT_UNIT_0,
    .filter = ENCODER_DEFAULT_FILTER};

  encoder2_handle = {
    .quad_pin_a = PIN_ENCODER2_QUAD_A,
    .quad_pin_b = PIN_ENCODER2_QUAD_B,
    .pcnt_unit = pcnt_unit_t::PCNT_UNIT_1,
    .filter = ENCODER_DEFAULT_FILTER};

  //error checks handled inside init functions
  current_sensor_init();

  encoder_init(&encoder1_handle);
  encoder_init(&encoder2_handle);

  motor_init(&motor1_handle);
  motor_init(&motor2_handle);

  motor_set_state(&motor1_handle, motor_state_t::MOTOR_LOW);
  motor_set_state(&motor2_handle, motor_state_t::MOTOR_LOW);

  //start communication tasks on core 0
  xTaskCreatePinnedToCore(
    TaskReadTCommands
    ,  "TReadCommands"
    ,  8192
    ,  NULL
    , TASK_PRIORITY_COMMAND
    , &xCommandTask
    , CORE_SERIAL_READ_TASK
  );
  ESP_LOGI(TAG, "Command Task Initialized. Task Status: %i\n",eTaskGetState(xCommandTask));

  //start telemetry on core 0
  xTaskCreatePinnedToCore(
    TaskPublishTelemetry
    ,  "Controller Publish Telemetry"
    ,  8192
    ,  NULL
    , TASK_PRIORITY_TELEMETRY
    , &xTelemTask
    , CORE_SERIAL_WRITE_TASK
  );
  ESP_LOGI(TAG, "Telemetry Task Initialized. Task Status: %i\n",eTaskGetState(xTelemTask));
  
  //start task
  xTaskCreatePinnedToCore(
    TaskRunTControl
    ,  "Twiddlerino T Control"
    ,  8192
    ,  NULL
    ,  TASK_PRIORITY_CONTROL
    ,  &xTControlTask
    ,  CORE_CONTROL_TASK
  );
  ESP_LOGI(TAG, "Control Task Initialized. Task Status: %i\n",eTaskGetState(xTControlTask));
}

/******************************************************************************/
/*                      P R I V A T E  F U N C T I O N S                      */
/******************************************************************************/

void TaskPublishTelemetry(void *pvParameters) {
  if(!Serial) {
    Serial.begin( UART_BAUD_RATE );
    ESP_LOGI(TAG, "Serial connected on uart0!" );
  }

  telemetry_t t;
  uint64_t last_time = millis();

  for(;;) 
  {
    if(enable_debug_telemetry && Serial.availableForWrite() && (xQueueReceive(xQueueTelemetry, &t, 20) == pdTRUE)){
      publish_telemetry_serial_studio(&t);
    }

    if (millis() > last_time + FREE_RTOS_TELEM_SAMPLE_RATE) {
      ESP_LOGI(TAG, "Number of freertos tasks running: %i", uxTaskGetNumberOfTasks());
      TaskHandle_t handle_arr[3] = {xCommandTask, xTelemTask, xTControlTask};
      for(int i=0;i<3;i++){
        auto name = pcTaskGetName(handle_arr[i]);
        auto mem = uxTaskGetStackHighWaterMark(handle_arr[i]);
        auto state = eTaskStateGet(handle_arr[i]);
        ESP_LOGI(TAG, "Task Status:\n\t*name:%s\tStatus:%i\tFree Stack Space:%u",
        name, state, mem);
      }

      last_time = millis();
    }

    vTaskDelay( 1 );
  }
}

void TaskRunTControl(void *pvParameters){
  if(!Serial) {
    Serial.begin( UART_BAUD_RATE );//this is on rx0 tx0
    ESP_LOGI(TAG, "Serial connected on uart0!" );
  }

  ESP_LOGI(TAG, "T Control Task Initialized.\n");

  //there's probably a better way to write the following section
  // and name the variables
  //this is prone to typos :)
  INIT_CONTROLLER_CONFIG_PARTIAL(default_config);
  controller1_handle->config = default_config;
  controller1_handle->ctrl_id = TWID1_ID;
  controller1_handle->telem_queue_handle = xQueueTelemetry;
  controller1_handle->motor_handle = &motor1_handle;
  controller1_handle->encoder_handle = &encoder1_handle;
  controller1_handle->current_sens_chan = curr_sens_adc_channel_t::CURRENT_SENSOR_1;
  tcontrol_init(controller1_handle, &(controller1_handle->config));
  tcontrol_start(controller1_handle);
  ESP_LOGI(TAG, "Controller %s loop status: %i\n", controller1_handle->ctrl_id,  tcontrol_is_running(controller1_handle));

  if (ENABLE_SECOND_CONTROLLER) {
    controller2_handle->config = default_config;
    controller2_handle->ctrl_id = TWID2_ID;
    controller2_handle->telem_queue_handle = xQueueTelemetry;
    controller2_handle->motor_handle = &motor2_handle;
    controller2_handle->encoder_handle = &encoder2_handle;
    controller2_handle->current_sens_chan = curr_sens_adc_channel_t::CURRENT_SENSOR_2;

    tcontrol_init(controller2_handle, &(controller2_handle->config));
    tcontrol_start(controller2_handle);

    ESP_LOGI(TAG, "Controller %s loop status: %i\n", controller2_handle->ctrl_id,  tcontrol_is_running(controller2_handle));
  }

  for(;;)
  {
    vTaskDelay(10);
  }
}

void TaskReadTCommands(void *pvParameters) {
  if(!Serial) {
    Serial.begin( UART_BAUD_RATE );//this is on rx0 tx0
    ESP_LOGI(TAG, "Serial connected on uart0!" );
  }

  String read_string;
  ESP_LOGI(TAG, "Update Control Params Task Started\n");
  cmd_type_t last_cmd = NA_CMD;

  for(;;) 
  {
    if (!Serial) {
      Serial.end();
      Serial.begin( UART_BAUD_RATE );
    }
    //check if any new bytes received in uart buffer
    if( Serial.available()) {
      read_string = read_string_until('\n');
      last_cmd = cmd_type_t::NA_CMD;
      ESP_LOGD(TAG, "Received data: %s\n", read_string);
      last_cmd = handle_command(&read_string);
      ack_cmd(last_cmd);
    }

    vTaskDelay( 10 );
  }
}

void enable_telemetry_publisher() {
  enable_debug_telemetry = true;
}

void disable_telemetry_publisher() {
    enable_debug_telemetry = false;
}

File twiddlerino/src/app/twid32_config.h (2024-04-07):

/**
 * @file twid32_config.h
 * @brief static default config for twid32
 * @author Yousif El-Wishahy (ywishahy@student.ubc.ca)
 * 
 */

#ifndef TWID32_CONFIG_H_
#define TWID32_CONFIG_H_

/******************************************************************************/
/*                              I N C L U D E S                               */
/******************************************************************************/
//need to import controller config struct definition
#include "app/control/control_types.h"

#include "twid32_pin_defs.h"

#include <FreeRTOSConfig.h>

/******************************************************************************/
/*                               D E F I N E S                                */
/******************************************************************************/

//twid ids
#define TWID1_ID "CONTROL_ONE"
#define TWID2_ID "CONTROL_TWO"

//command and telemetry config
#define ENABLE_DEBUG_TELEMETRY_ON_INIT true
#define TELEMETRY_QUEUE_SIZE 250U
#define TELEMETRY_DEFAULT_SAMPLE_RATE 20U //telemetry sample rate in (control loops)/sample
#define FREE_RTOS_TELEM_SAMPLE_RATE 5000U //MS

#define ENABLE_SECOND_CONTROLLER 1

//hardware config
//encoder
#define ENCODER_DEFAULT_FILTER 200
#define ENCODER_CPR 500

//serial port
#define UART_BAUD_RATE 1000000U

//motor
#define MOTOR_MAX_SPEED_RPM 100000
#define MOTOR_PWM_FREQ 20000U
#define MOTOR_DUTY_CYCLE_RES_BITS 10U
#define MOTOR_DUTY_CYCLE_RES 1024
#define MOTOR1_PWM_CHAN_DEFAULT 0
#define MOTOR2_PWM_CHAN_DEFAULT 2

//current sensor
#define CURRENT_SENS_VOLTS_PER_AMP 0.136 //mV/Amp sensitivity on the hall effect sensor

//macro for struct (partial) init to fill out default controller parameters
//CHANGE CONTROLLER DEFAULT CONFIG HERE!!!!
#define INIT_CONTROLLER_CONFIG_PARTIAL(X) controller_config_t X = {\
    .control_type = control_type_t::POSITION_CTRL,\
    .setpoint_type = setpoint_type_t::CONSTANT_SETPOINT_MODE,\
    .init_setpoint = {.pos = 0.0, .vel = 0.0, .accel = 0.0, .torque = 0.0},\
    .controller_direction = controller_direction_t::NEGATIVE_FEEDBACK,\
    .sample_time_us = 1000,\
    .Kp = 0.5, .Ki = 0.01, .Kd = 0.01, .N = 1.0,\
    .velocity_filter_const = 0.01,\
    .current_filter_const = 0.1,\
    .motor_Kv = 2E-5, .motor_Ke = 0.009901879421645426, .motor_J = 1e-6,\
    .impedance = {.K = 1e-3, .B = 0.01, .J = 1e-6},\
    .output_hlim = MOTOR_DUTY_CYCLE_RES, .output_llim = -MOTOR_DUTY_CYCLE_RES,\
    .telemetry_sample_rate = TELEMETRY_DEFAULT_SAMPLE_RATE,\
}

//freertos config
#define CORE_CONTROL_TASK 1U
#define CORE_SENSOR_TASK 1U
#define CORE_SERIAL_READ_TASK 0U
#define CORE_SERIAL_WRITE_TASK 0U

#define TASK_PRIORITY_CONTROL (configMAX_PRIORITIES - 1)
#define TASK_PRIORITY_TELEMETRY (configMAX_PRIORITIES - 1)
#define TASK_PRIORITY_GAME_SEND (configMAX_PRIORITIES - 1)
#define TASK_PRIORITY_COMMAND (configMAX_PRIORITIES)
#define TASK_PRIORITY_SENSOR (configMAX_PRIORITIES)

#endif // TWID32_CONFIG_H_

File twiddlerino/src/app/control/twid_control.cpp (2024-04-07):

/**
 * @file twid_control.c
 * @brief Control class for implementing the various controllers for the twiddlerino
 * @author Yousif El-Wishahy (ywishahy@student.ubc.ca)
 */

/******************************************************************************/
/*                              I N C L U D E S                               */
/******************************************************************************/

//header for this file
#include "app/control/twid_control.h"

//config
#include "app/twid32_config.h"

//hardware drivers
#include "drivers/encoder.h"
#include "drivers/motor.h"
#include "drivers/current_sensor.h"

//filters
#include "app/filter/ewma_filter.h"

//calibration
#include "app/calibration/motor_lut.h"

//comms
#include "app/comms.h"

/******************************************************************************/
/*                               D E F I N E S                                */
/******************************************************************************/

#define DEGS_TO_RPM 0.1666667
#define _ENTER_CRITICAL() portENTER_CRITICAL_SAFE(&spinlock)
#define _EXIT_CRITICAL() portEXIT_CRITICAL_SAFE(&spinlock)

/******************************************************************************/
/*                              T Y P E D E F S                               */
/******************************************************************************/


/******************************************************************************/
/*            P R I V A T E  F U N C T I O N  P R O T O T Y P E S             */
/******************************************************************************/

static void pid_callback(void *arg);

static void debug_print_cfg(twid_controller_t*);

/******************************************************************************/
/*               P R I V A T E  G L O B A L  V A R I A B L E S                */
/******************************************************************************/
//logtag
static const char* TAG = "twid_control";

static twid_controller_t controller_1;
static twid_controller_t controller_2;
twid_controller_t *controller2_handle = &controller_1;
twid_controller_t *controller1_handle = &controller_2;

static portMUX_TYPE spinlock = portMUX_INITIALIZER_UNLOCKED;

/******************************************************************************/
/*                       P U B L I C  F U N C T I O N S                       */
/******************************************************************************/

void tcontrol_init(twid_controller_t* ctrl_handle, controller_config_t* config) {
    // if(tcontrol_is_running(ctrl_handle)){
    //     tcontrol_stop(ctrl_handle);
    // }
    motor_set_state(ctrl_handle->motor_handle, motor_state_t::MOTOR_LOW);
    encoder_clear_count(ctrl_handle->encoder_handle);

    ctrl_handle->mutex = xSemaphoreCreateMutex();
    ctrl_handle->config = *config;
    ctrl_handle->setpoint = {.pos = 0.0, .vel =0.0, .accel = 0.0};
    ctrl_handle->last_time = 0;
    ctrl_handle->start_time = 0;
    ctrl_handle->telem_dt = 0;
    ctrl_handle->last_pos = 0;
    ctrl_handle->itr = 0;
    ctrl_handle->velocity_filt_ewa = EwmaFilter(ctrl_handle->config.velocity_filter_const, 0.0);
    ctrl_handle->current_filt_ewa = EwmaFilter(ctrl_handle->config.current_filter_const, 0.0);
    ctrl_handle->pid_controller = DiscretePID(&ctrl_handle->config);
    ctrl_handle->telem.current_sps = current_sensor_sps();
    ctrl_handle->telem.nframes_sent_queue = 0;

    const esp_timer_create_args_t timer_args = {
        .callback = pid_callback,
        .arg = ctrl_handle,
        .name = "pid_loop"
    };

    if(ctrl_handle->pid_timer == NULL){
        ESP_ERROR_CHECK(esp_timer_create(&timer_args, &ctrl_handle->pid_timer));
    }

    ESP_LOGI(TAG, "controller config complete");
    debug_print_cfg(ctrl_handle);
}

void tcontrol_start(twid_controller_t* ctrl_handle){
    _ENTER_CRITICAL();
    ESP_LOGD(TAG, "%s starting", ctrl_handle->ctrl_id);
    if(!esp_timer_is_active(ctrl_handle->pid_timer)) {
        ctrl_handle->last_time = micros();
        ctrl_handle->start_time = micros();
        ESP_ERROR_CHECK(esp_timer_start_periodic(ctrl_handle->pid_timer, ctrl_handle->config.sample_time_us));
        ESP_LOGD(TAG, "Started pid callback for controller %s with timer with period %lu", ctrl_handle->ctrl_id, ctrl_handle->config.sample_time_us);
    }
    _EXIT_CRITICAL();
}

void tcontrol_stop(twid_controller_t* ctrl_handle){
    _ENTER_CRITICAL();
    if(esp_timer_is_active(ctrl_handle->pid_timer)) {
        ESP_ERROR_CHECK(esp_timer_stop(ctrl_handle->pid_timer));
        ESP_LOGW(TAG, "stopped control loop with id: %s", ctrl_handle->ctrl_id);
    }
    _EXIT_CRITICAL();
}

void tcontrol_reset(twid_controller_t* ctrl_handle){
    _ENTER_CRITICAL();
    ESP_LOGD(TAG, "tcontrol_reset called for id: %s", ctrl_handle->ctrl_id);
    tcontrol_stop(ctrl_handle);
    INIT_CONTROLLER_CONFIG_PARTIAL(def);
    ctrl_handle->config = def;
    tcontrol_init(ctrl_handle, &ctrl_handle->config);
    tcontrol_start(ctrl_handle);
    _EXIT_CRITICAL();
}

bool tcontrol_is_running(twid_controller_t* ctrl_handle){
    return esp_timer_is_active(ctrl_handle->pid_timer);
}

void tcontrol_update_setpoint(twid_controller_t* ctrl_handle, setpoint_t* tp) {
    _ENTER_CRITICAL();
    ctrl_handle->setpoint = *tp;
    ESP_LOGD(TAG, "Updated control setpoint to %lf, %lf, %lf, %lf",
    ctrl_handle->setpoint.pos, ctrl_handle->setpoint.vel, ctrl_handle->setpoint.accel, ctrl_handle->setpoint.torque);
    debug_print_cfg(ctrl_handle);
    _EXIT_CRITICAL();
}

void tcontrol_update_cfg(twid_controller_t* ctrl_handle, controller_config_t* cfg) {
    _ENTER_CRITICAL();
    ctrl_handle->config.Kp = cfg->Kp;
    ctrl_handle->config.Ki = cfg->Ki;
    ctrl_handle->config.Kd = cfg->Kd;
    ctrl_handle->config.impedance.K = cfg->impedance.K;
    ctrl_handle->config.impedance.J = cfg->impedance.J;
    ctrl_handle->config.impedance.B = cfg->impedance.B;
    ctrl_handle->config.control_type = cfg->control_type;
    ctrl_handle->config.telemetry_sample_rate = cfg->telemetry_sample_rate;
    ctrl_handle->pid_controller.set_all_params(&ctrl_handle->config);
    debug_print_cfg(ctrl_handle);
    _EXIT_CRITICAL();
}

/******************************************************************************/
/*                      P R I V A T E  F U N C T I O N S                      */
/******************************************************************************/
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

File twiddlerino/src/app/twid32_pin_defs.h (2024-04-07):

/**
 * @file twid32_pin_defs.h
 * @brief pin definitions for esp32 io
 * @author Yousif El-Wishahy (ywishahy@student.ubc.ca)
 * 
 */

#ifndef TWID32_PIN_DEFS_H_
#define TWID32_PIN_DEFS_H_

/******************************************************************************/
/*                              I N C L U D E S                               */
/******************************************************************************/

#include "hal/gpio_types.h"

/******************************************************************************/
/*                               D E F I N E S                                */
/******************************************************************************/

//encoders
#define PIN_ENCODER1_QUAD_A  gpio_num_t::GPIO_NUM_26  //Encoder 1 quaderture signal A
#define PIN_ENCODER1_QUAD_B  gpio_num_t::GPIO_NUM_25   //Encoder 1 quaderture signal B

#define PIN_ENCODER2_QUAD_A  gpio_num_t::GPIO_NUM_4  //Encoder 2 quaderture signal A
#define PIN_ENCODER2_QUAD_B  gpio_num_t::GPIO_NUM_27   //Encoder 2 quaderture signal B

//current sensor (communicates through i2c interface)
#define PIN_CURRENT_SENS_ADC_SCL  gpio_num_t::GPIO_NUM_22
#define PIN_CURRENT_SENS_ADC_SDA  gpio_num_t::GPIO_NUM_21
#define PIN_CURRENT_SENS_ADC_ALERT gpio_num_t::GPIO_NUM_19

//motors
#define PIN_MOTOR1_POWER     gpio_num_t::GPIO_NUM_16  //motor 1 power (pwm) signal
#define PIN_MOTOR1_DIR       gpio_num_t::GPIO_NUM_17  //motor 1 dir pin

#define PIN_MOTOR2_POWER     gpio_num_t::GPIO_NUM_23  //motor 2 power (pwm) signal
#define PIN_MOTOR2_DIR       gpio_num_t::GPIO_NUM_32  //motor 2 dir pin

#endif // TWID32_PIN_DEFS_H_

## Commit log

2024-01-31 esp32 code for twid shield interfacing and control, second core used for comms
2024-02-04 updates to esp32 code for testing and telemetry
2024-02-05 Created encoder library to decode encoder signals directly on cpu as opposed to external ic, reduced io lines from 11 to 2 :)
2024-02-08 fixed build errors relating to naming of functions and undefined functions VtakGetInfo
    [comms.cpp, comms.h, motor.cpp]
2024-02-11 added current sensing from gavin's branch and refactored
2024-03-07 fixed thresholding logic bug and motor direction bug in motor driving code, updates to telemetry code
    [comms.cpp, comms.h, current_sensor.cpp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]
2024-03-08 Changes made to get circuit to work in Mar 6 work session
2024-03-08 timer interrupt based controller
2024-03-09 finished updated pid controller, stop/reset over serial, more telemetry, torque estimation. All that is left is calibration and impedance,admittance switching
    [comms.cpp, comms.h, current_sensor.cpp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]
2024-03-09 discrete pid class
2024-03-10 current sens background task
2024-03-11 added frame header to telemetry config
2024-03-14 fixed reset error check causing crash
    [comms.cpp, twid_control.cpp]
2024-03-14 added 'no control' mode, and added direct set of pwm duty cycle
2024-03-14 motor speed safety check
2024-03-20 game interface c (esp32) and python (pc) implementation
2024-03-20 pin def for encoders
2024-03-20 higher baud rate, config for output signal correction, more info in game telemetry dataclass
    [main.py, twid32_config.h, twid_control.cpp]
2024-03-21 renamed interface class and made it fully compatible with serial studio telemetry frames
2024-03-22 initial calibration curve for dc to current draw (no load)
2024-03-22 added torque estimation using lookup table. Removed virtual env code, not used anymore.
2024-03-22 fixed comms receive bugs, added update sample rate, fixed serial interface decoding logic
    [comms.cpp, motor_lut.cpp, serial_interface.py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]
2024-03-22 calibration test for determining resistance and motor constant
2024-03-28 motor and current sensor driver updates for new hbridge circuit
2024-03-28 Socket server updates
2024-03-29 current sensor driver changes for new lin. hall effect sensor
2024-03-31 current sensor firmware updates for hall sensor, added adc telemetry signal
2024-03-31 added alert adc pin to pin config
2024-03-31 current sens driver interrupt and telem script update
2024-03-31 config i2c clock after bus init
2024-04-01 current step response system identification
2024-04-04 added extensive logging to esp32
2024-04-05 minor logging changes and added reboot test
    [serial_interface.py]
2024-04-05 removed unused init config in firmware, better logging across all firmware modules, removed setpoint buffer causing memory leaks
    [comms.cpp, motor.cpp, twid32_config.h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]
2024-04-05 rebased hardware driver changes onto logger changes
2024-04-05 swapped encoder pin definitions to match test board
    [twid32_pin_defs.h]
2024-04-05 calibration and config changes made during testing, see test logs for details
2024-04-06 transfer function for position and velocity obtained
2024-04-07 readme changes and added pcb
    [ESP32Twiddlerino.kicad_pcb, ESP32Twiddlerino.kicad_sch, LogicLevelConverter.kicad_sch]
2024-04-07 Add files via upload
    Most recent version of switching between admittance and impedance control
2024-04-09 added test bench schematic and component libs
    [100SP1T2B4M6QE.step, 20021511-00010T4LF.step, 2311765-1.step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]
2024-04-09 updated schematic title and added pdf
    [TestBench.kicad_sch]
2024-04-09 Added pdf of PCB schematic
